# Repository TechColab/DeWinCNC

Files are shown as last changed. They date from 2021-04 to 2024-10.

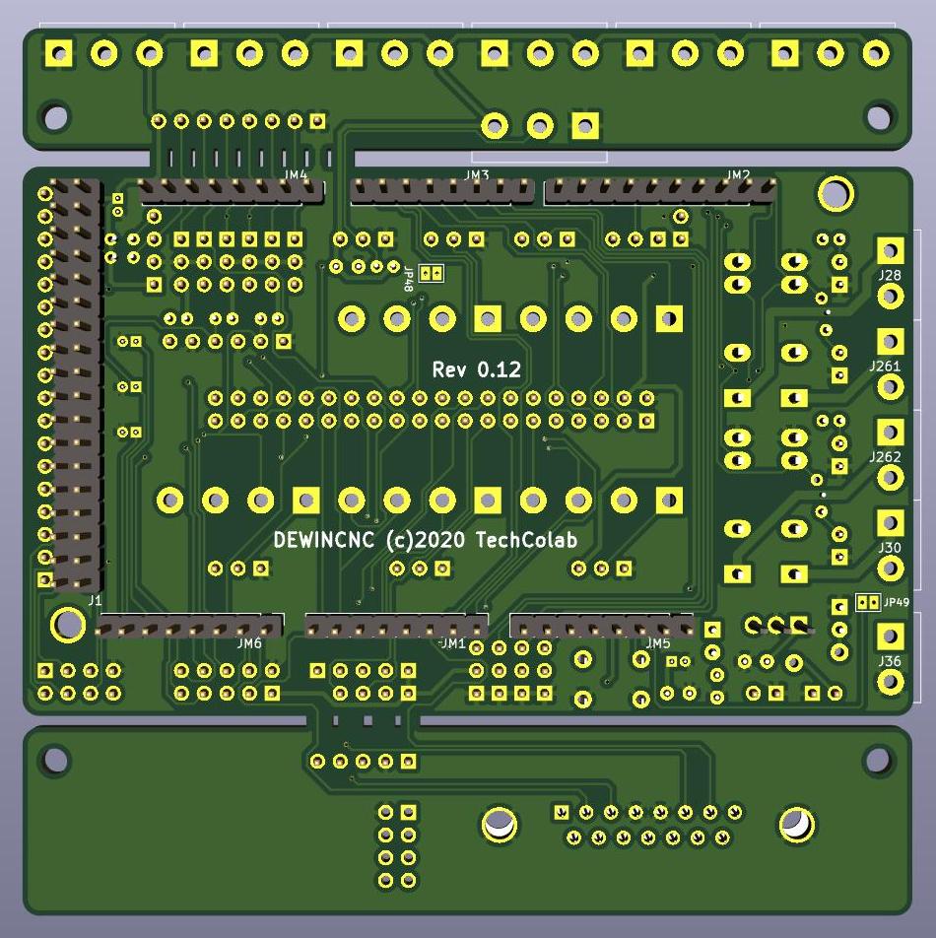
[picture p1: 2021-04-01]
DeWinCNC-B.jpg

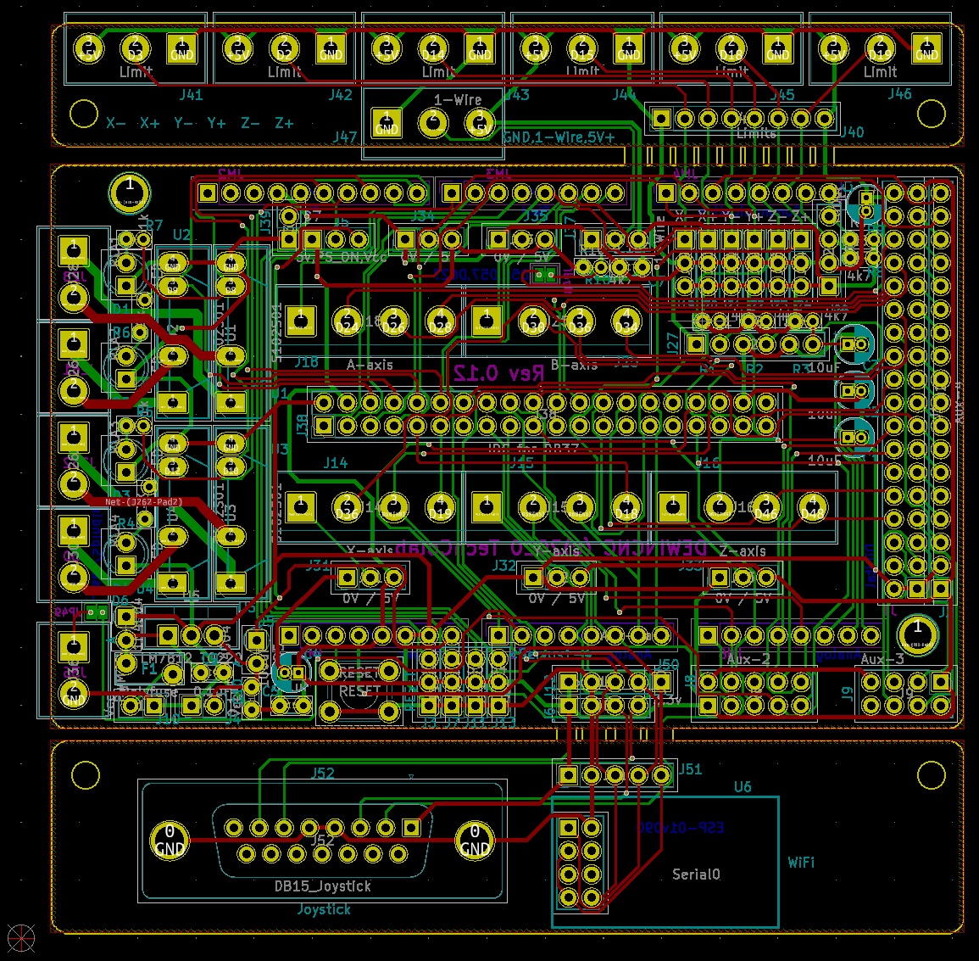
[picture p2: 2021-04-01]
DeWinCNC-PCBjpg.jpg

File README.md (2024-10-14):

DeWinCNC brings the benefits of the RAMPS eco-system to machines which originated with WinCNC.

Compared with WinCNC:
WinCNC software uses a proprietory daughter card on a full-size PCI I/O card which needs a Windows desktop PC.

This shield + an Arduino MEGA 2560 + Marlin firmware enables you to use a laptop of any OS you like, 
with a choice of controller/loader apps.  Or no computer at all - just load files from an SD-card!

You can use entirely open source software with no license or on-going maintenance costs.
Or you can chose somehting like LightBurn which has a great camera feature at a great price.

In common with WinCNC:
Includes the same DB37 plug for direct connection to your existing machne's breakout board.

Compared with RAMPS:
Uses common industrial off-board stepper driver modules so you can scale to any power your mechine needs.

Has a 1-Wire interface so you can use as many digital temperature sensors as you like.

Has 4 on-board isolated SolidState Relays for switching machine power, GasAssist, VacuumPump etc.

Can take power entirely from the USB host, or from a common industrial 24Vdc supply.

Limit switch inputs have convenient screw-terminal connectors.

In common with RAMPS:
Limit switch headers, I2C & reset botton.
Keeps the Aux-1,2,3,4 ports for Servos, SD-card, LCD contoler etc. within the same footprint.

Additional functionality:
Could be plugged into the WinCNC controller to replace the CNC machine's breakout board.
Could be used with the WinCNC controller to monitor/simulate most signals.
Can be used as a general purpose breakout shield with 4 SSRs & 23 I/O lines (inc 10 analog).

ToDo:
Most PCB manufacturers will want a bigger gap between main & break-off boards.  And perforation holes.

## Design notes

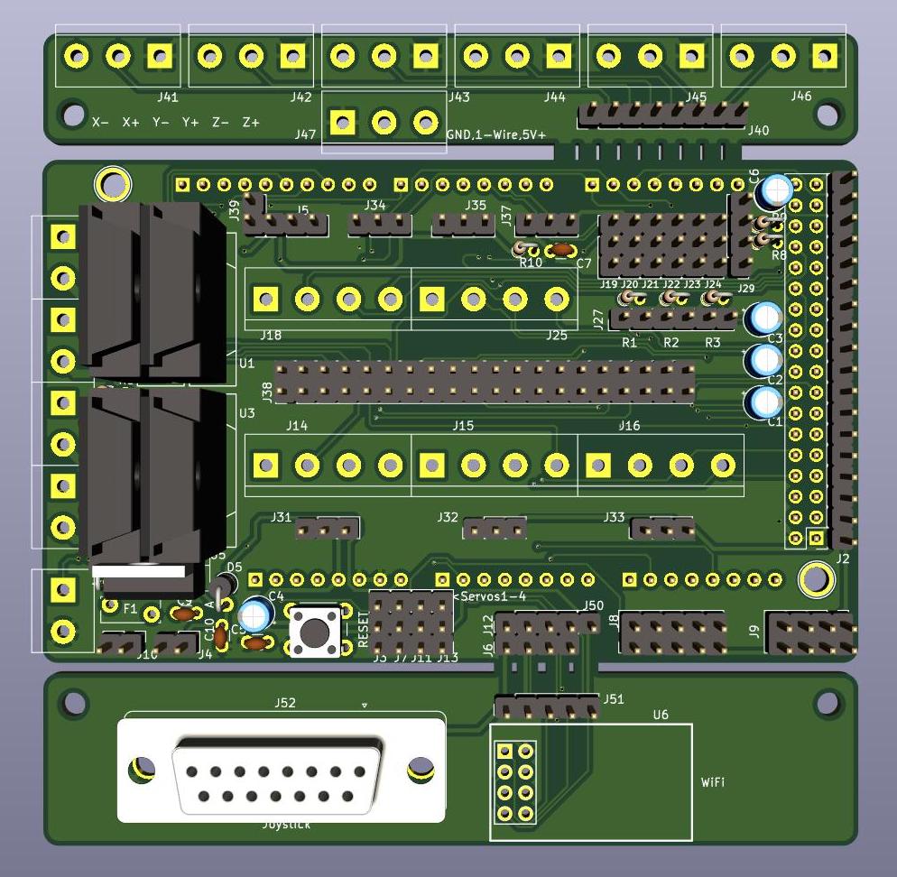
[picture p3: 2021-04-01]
DeWinCNC-F.jpg

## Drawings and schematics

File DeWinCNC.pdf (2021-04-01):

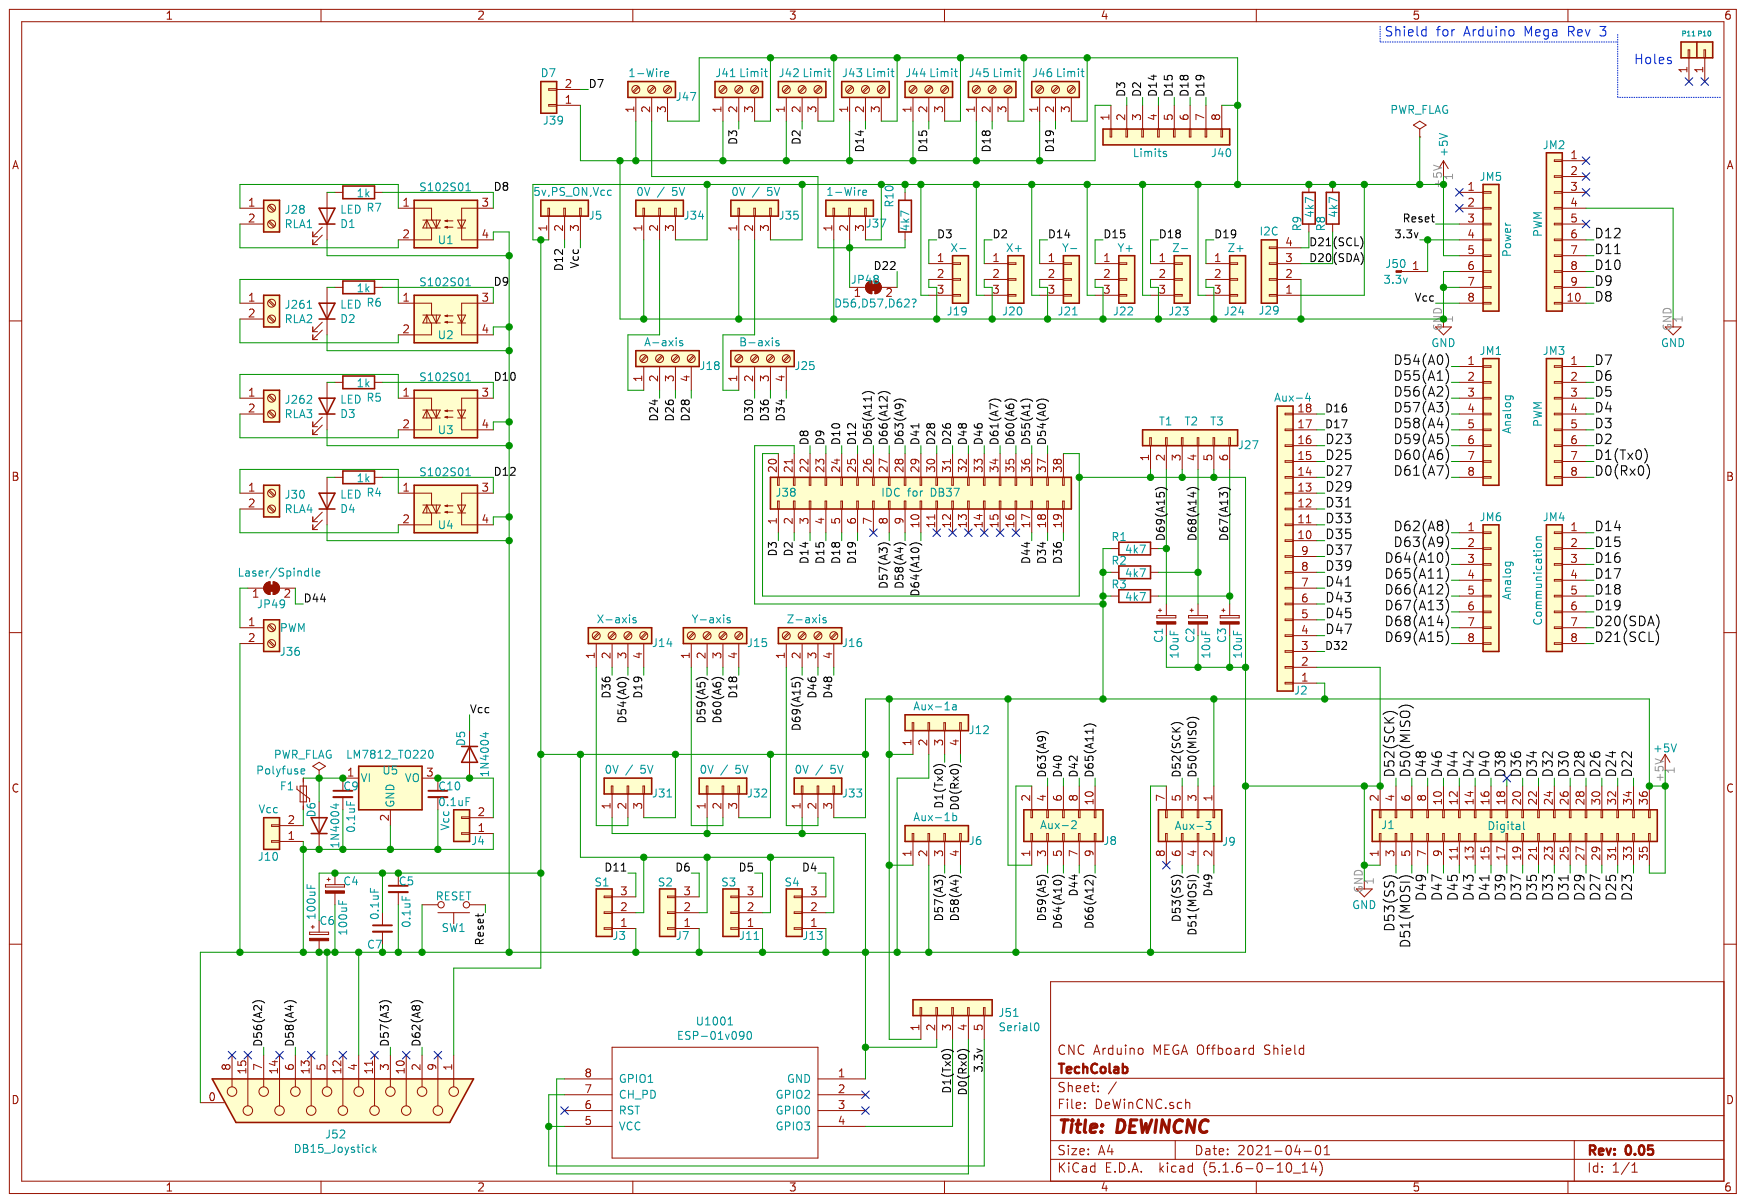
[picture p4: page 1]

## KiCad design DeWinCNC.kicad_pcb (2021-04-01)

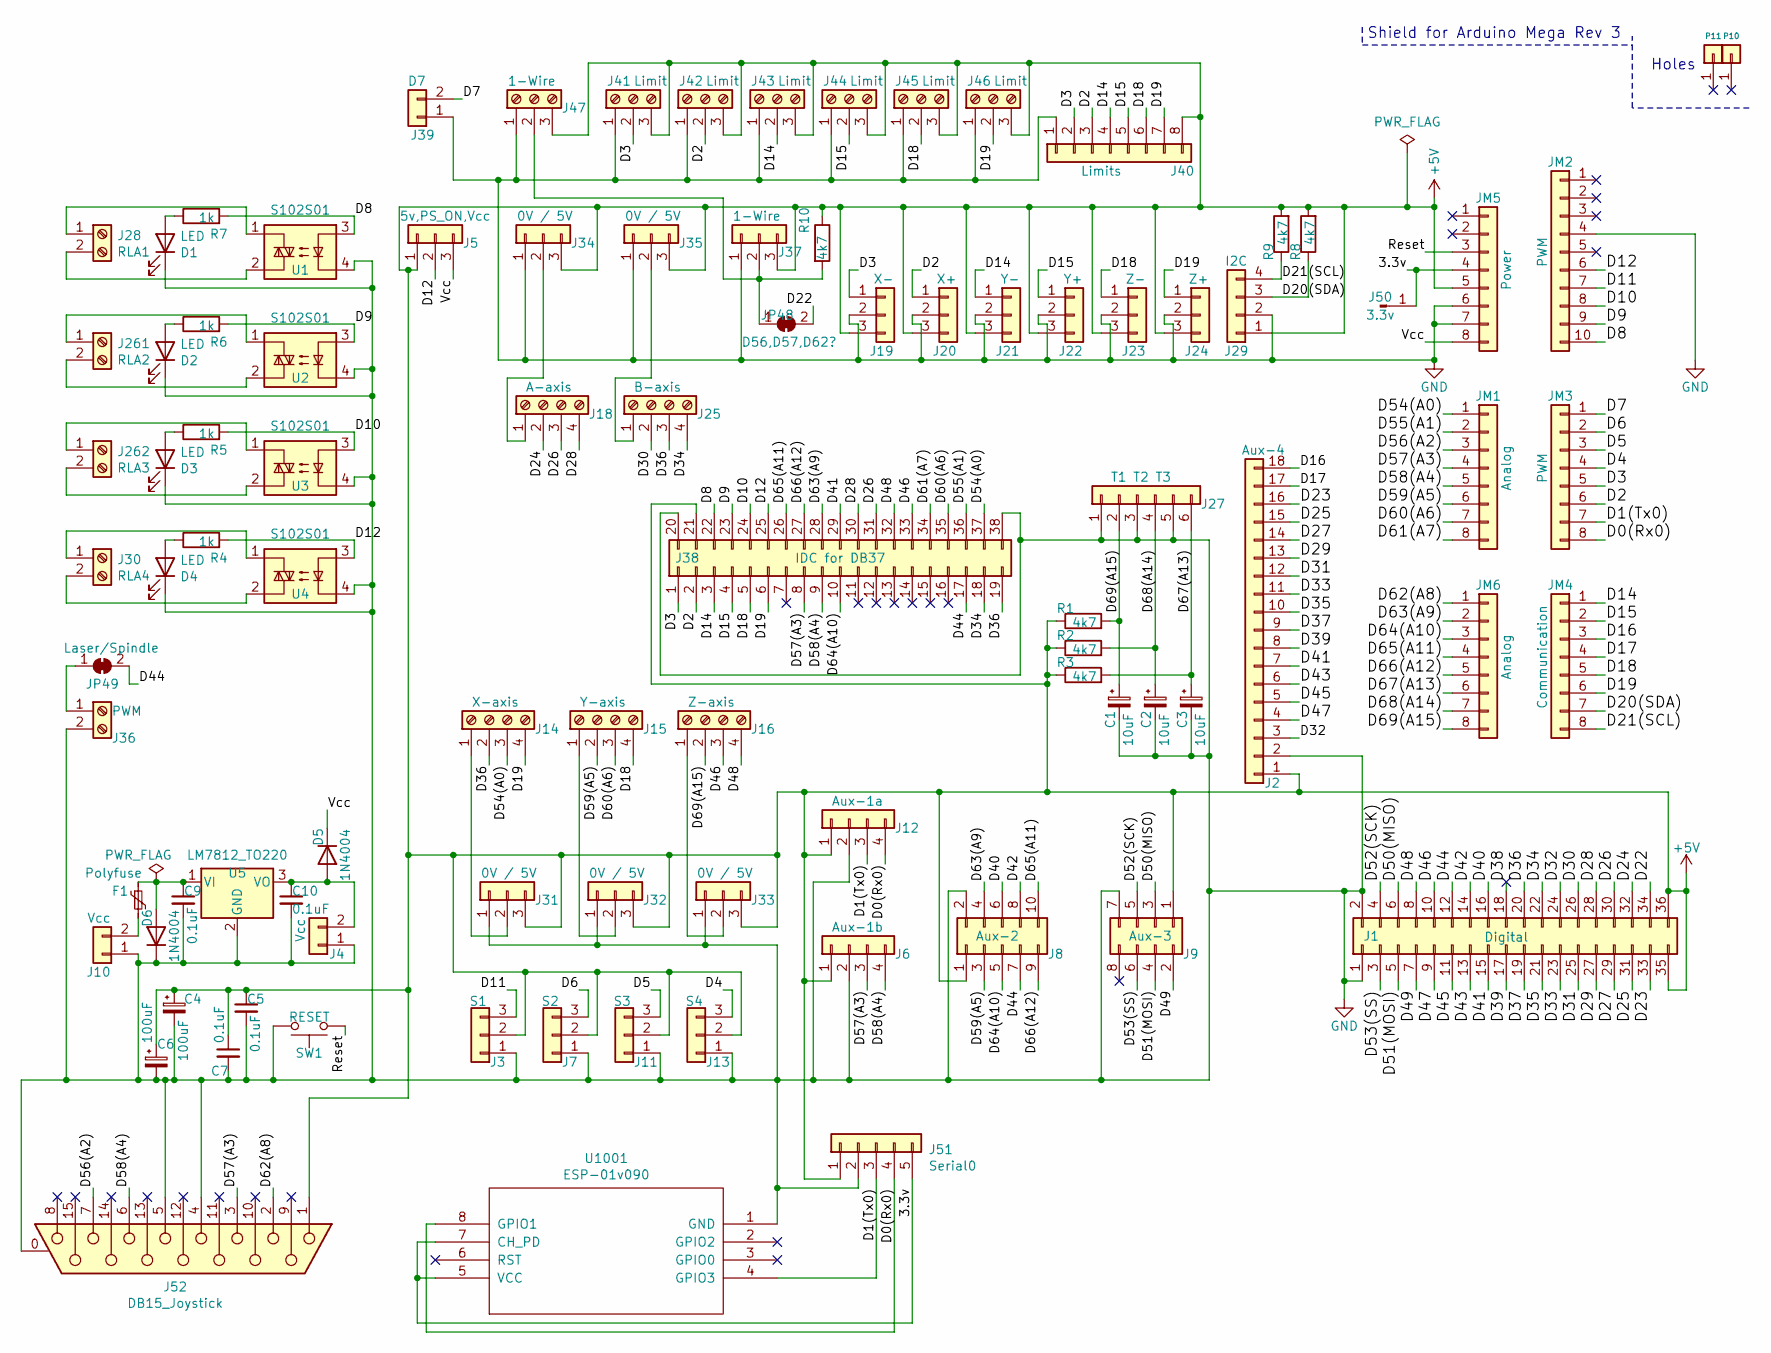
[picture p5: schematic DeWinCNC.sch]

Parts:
C1, C2, C3: 10uF
C4, C6: 100uF
C5, C7, C9, C10: 0.1uF
D1, D2, D3, D4: LED
D5, D6: 1N4004; D_DO-41_SOD81_P10.16mm_Horizontal
F1: Polyfuse
J1: Digital; Socket_Strip_Arduino_2x18
J2: Aux-4
J3: S1
J4, J10: Vcc
J5: 5v,PS_ON,Vcc
J6: Aux-1b
J7: S2
J8: Aux-2
J9: Aux-3
J11: S3
J12: Aux-1a
J13: S4
J14: X-axis
J15: Y-axis
J16: Z-axis
J18: A-axis
J19: X-
J20: X+
J21: Y-
J22: Y+
J23: Z-
J24: Z+
J25: B-axis
J27: T1 T2 T3
J28: RLA1
J29: I2C
J30: RLA4
J31, J32, J33, J34, J35: 0V / 5V
J36: PWM
J37, J47: 1-Wire
J38: IDC for DB37
J39: D7
J40: Limits; Socket_Strip_Arduino_1x08
J41, J42, J43, J44, J45, J46: Limit
J50: 3.3v
J51: Serial0
J52: DB15_Joystick
J261: RLA2
J262: RLA3
JM1, JM6: Analog; Socket_Strip_Arduino_1x08
JM2: PWM; Socket_Strip_Arduino_1x10
JM3: PWM; Socket_Strip_Arduino_1x08
JM4: Communication; Socket_Strip_Arduino_1x08
JM5: Power; Socket_Strip_Arduino_1x08
JP48: D56,D57,D62?
JP49: Laser/Spindle
P10, P11: CONN_01X01; Arduino_1pin
R1, R2, R3, R8, R9, R10: 4k7
R4, R5, R6, R7: 1k
SW1: RESET
U1, U2, U3, U4: S102S01; SIP4_Sharp-SSR_P7.62mm_Straight
U5: LM7812_TO220; TO-220-3_Vertical
U1001: ESP-01v090; PinSocket_2x04_P2.54mm_Vertical

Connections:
+5V: C4.1, C5.1, C6.1, C7.1, J1.35, J1.36, J2.1, J3.2, J5.1, J6.1, J7.2, J8.1, J9.1, J11.2, J12.1, J13.2, J19.3, J20.3, J21.3, J22.3, J23.3, J24.3, J29.1, J31.3, J32.3, J33.3, J34.3, J35.3, J37.3, J38.21, J40.8, J41.3, J42.3, J43.3, J44.3, J45.3, J46.3, J47.3, J51.1, J52.1, JM5.5, R1.1, R2.1, R3.1, R8.2, R9.2, R10.1
/3.3v: J50.1, J51.5, JM5.4, U1001.5 (VCC), U1001.7 (CH_PD); also elsewhere on the board
/D0(Rx0): J12.4, J51.4, JM3.8, U1001.8 (GPIO1); also elsewhere on the board
/D1(Tx0): J12.3, J51.3, JM3.7, U1001.4 (GPIO3); also elsewhere on the board
/D2: J20.1, J38.2, J40.3, J42.2, JM3.6
/D3: J19.1, J38.1, J40.2, J41.2, JM3.5
/D4: J13.3, JM3.4
/D5: J11.3, JM3.3
/D6: J7.3, JM3.2
/D7: J39.2, JM3.1
/D8: J38.22, JM2.10, R7.2, U1.3
/D9: J38.23, JM2.9, R6.2, U2.3
/D10: J38.24, JM2.8, R5.2, U3.3
/D11: J3.3, JM2.7
/D12: J5.2, J38.25, JM2.6, R4.2, U4.3
/D14: J21.1, J38.3, J40.4, J43.2, JM4.1
/D15: J22.1, J38.4, J40.5, J44.2, JM4.2
/D16: J2.18, JM4.3
/D17: J2.17, JM4.4
/D18: J15.4, J23.1, J38.5, J40.6, J45.2, JM4.5
/D19: J14.4, J24.1, J38.6, J40.7, J46.2, JM4.6
/D20(SDA): J29.3, JM4.7, R8.1
/D21(SCL): J29.4, JM4.8, R9.1
/D22: J1.34, JP48.2 (B)
/D23: J1.33, J2.16
/D24: J1.32, J18.2
/D25: J1.31, J2.15
/D26: J1.30, J18.3, J38.31
/D27: J1.29, J2.14
/D28: J1.28, J18.4, J38.30
/D29: J1.27, J2.13
/D30: J1.26, J25.2
/D31: J1.25, J2.12
/D32: J1.24, J2.3
/D33: J1.23, J2.11
/D34: J1.22, J25.4, J38.18
/D35: J1.21, J2.10
/D36: J1.20, J14.2, J25.3, J38.19
/D37: J1.19, J2.9
/D38: J1.18
/D39: J1.17, J2.8
/D40: J1.16, J8.6
/D41: J1.15, J2.7, J38.29
/D42: J1.14, J8.8
/D43: J1.13, J2.6
/D44: J1.12, J8.7, J38.17, JP49.2 (B)
/D45: J1.11, J2.5
/D46: J1.10, J16.3, J38.33
/D47: J1.9, J2.4
/D48: J1.8, J16.4, J38.32
/D49: J1.7, J9.2
/D50(MISO): J1.6, J9.3
/D51(MOSI): J1.5, J9.4
/D52(SCK): J1.4, J9.5
/D53(SS): J1.3, J9.6
/D54(A0): J14.3, J38.37, JM1.1
/D55(A1): J38.36, JM1.2
/D56(A2): J52.7, JM1.3
/D57(A3): J6.3, J38.8, J52.3, JM1.4
/D58(A4): J6.4, J38.9, J52.6, JM1.5
/D59(A5): J8.3, J15.2, JM1.6
/D60(A6): J15.3, J38.35, JM1.7
/D61(A7): J38.34, JM1.8
/D62(A8): J52.2, JM6.1
/D63(A9): J8.4, J38.28, JM6.2
/D64(A10): J8.5, J38.10, JM6.3
/D65(A11): J8.10, J38.26, JM6.4
/D66(A12): J8.9, J38.27, JM6.5
/D67(A13): C3.1, J27.6, JM6.6, R3.2
/D68(A14): C2.1, J27.4, JM6.7, R2.2
/D69(A15): C1.1, J16.2, J27.2, JM6.8, R1.2
/Reset: JM5.3, SW1.1; also elsewhere on the board
/Vcc: D5.1 (K), J5.3, JM5.8
GND: C1.2, C2.2, C3.2, C4.2, C5.2, C6.2, C7.2, C9.2, C10.2, D1.1 (K), D2.1 (K), D3.1 (K), D4.1 (K), D6.1 (K), J1.1, J1.2, J2.2, J3.1, J4.1, J6.2, J7.1, J8.2, J9.7, J10.1, J11.1, J12.2, J13.1, J19.2, J20.2, J21.2, J22.2, J23.2, J24.2, J27.1, J27.3, J27.5, J29.2, J31.1, J32.1, J33.1, J34.1, J35.1, J36.2, J37.1, J38.20, J38.38, J39.1, J40.1, J41.1, J42.1, J43.1, J44.1, J45.1, J46.1, J47.1, J51.2, J52.0 (PAD), J52.4, J52.5, JM2.4, JM5.6, JM5.7, SW1.2, U1.4, U2.4, U3.4, U4.4, U5.2 (GND), U1001.1 (GND); also elsewhere on the board
unnamed: C9.1, D6.2 (A), F1.1, U5.1 (VI)
unnamed: C10.1, D5.2 (A), J4.2, U5.3 (VO)
unnamed: D1.2 (A), R7.1
unnamed: D2.2 (A), R6.1
unnamed: D3.2 (A), R5.1
unnamed: D4.2 (A), R4.1
unnamed: F1.2, J10.2
unnamed: J14.1, J31.2
unnamed: J15.1, J32.2
unnamed: J16.1, J33.2
unnamed: J18.1, J34.2
unnamed: J25.1, J35.2
unnamed: J28.1, U1.1
unnamed: J28.2, U1.2
unnamed: J30.1, U4.1
unnamed: J30.2, U4.2
unnamed: J36.1, JP49.1 (A)
unnamed: J37.2, J47.2, JP48.1 (A), R10.2
unnamed: J261.1, U2.1
unnamed: J261.2, U2.2
unnamed: J262.1, U3.1
unnamed: J262.2, U3.2

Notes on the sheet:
Shield for Arduino Mega Rev 3
Holes

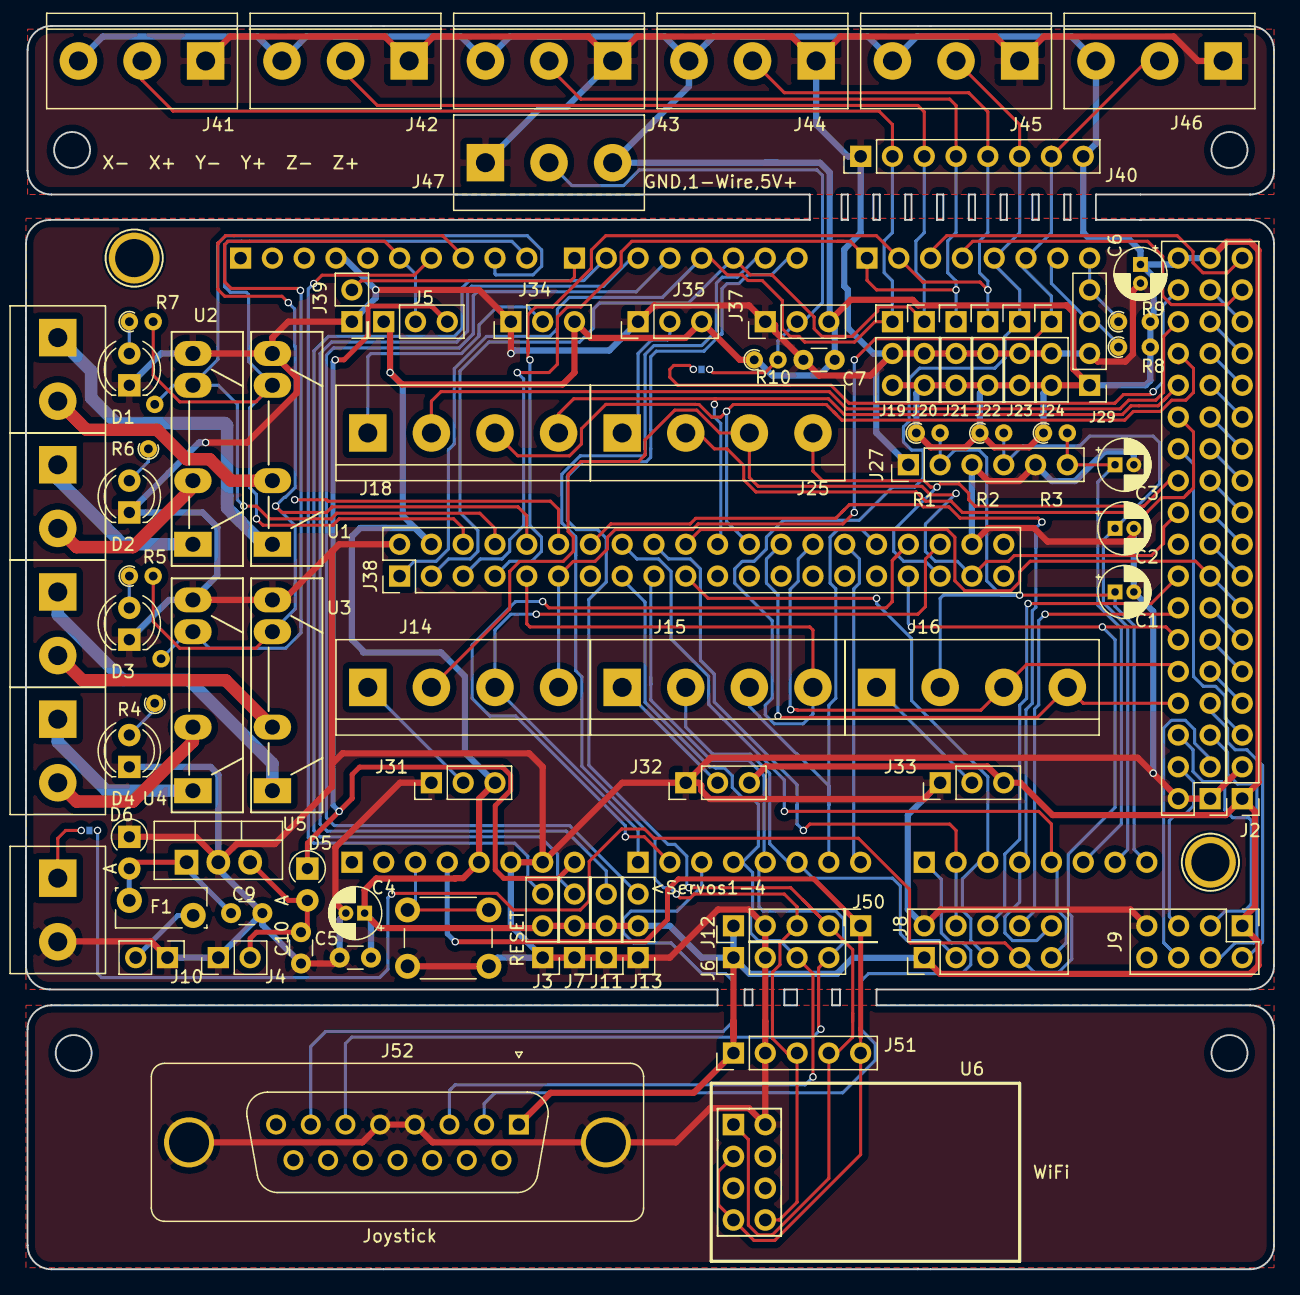
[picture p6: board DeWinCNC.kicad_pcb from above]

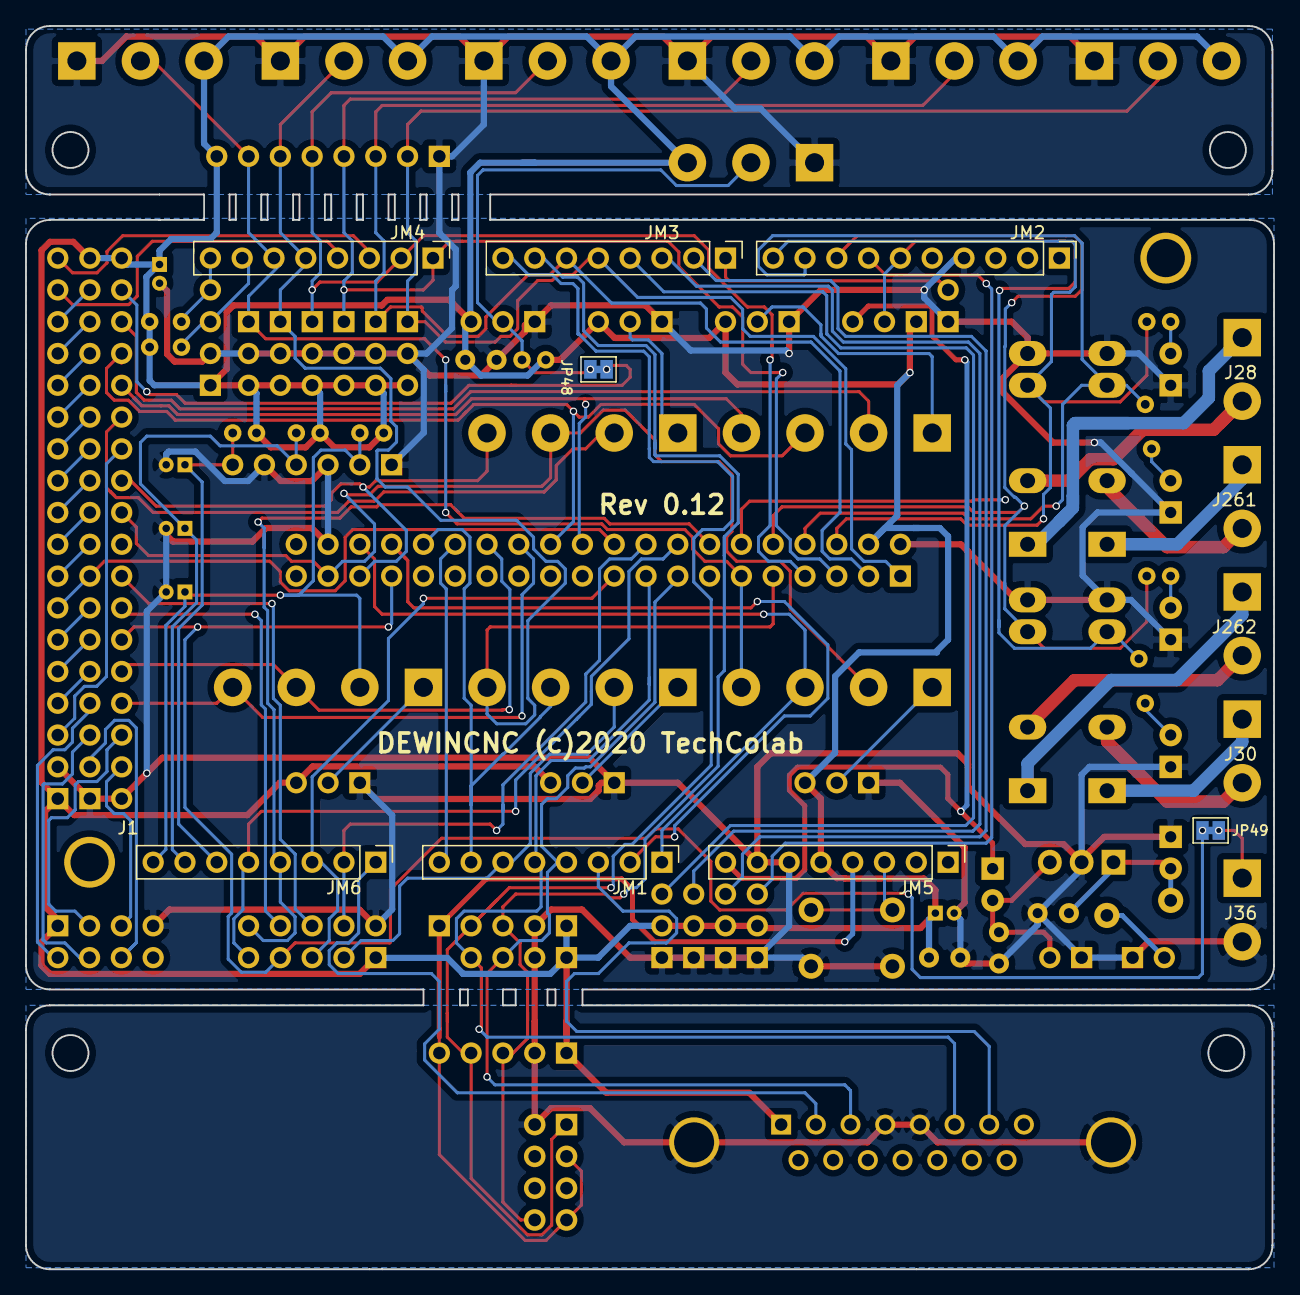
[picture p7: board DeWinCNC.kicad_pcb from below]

Board: 2 copper layers, 99.7 x 99.3 mm, 93 parts (9 on the bottom side), 95 nets.

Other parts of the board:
RESET: RESET; SW_PUSH_6mm_H4.3mm
U6: ESP-01v090; ESP-01

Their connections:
/3.3v: U6.3, U6.7; also elsewhere on the board
/D0(Rx0): U6.1; also elsewhere on the board
/D1(Tx0): U6.8; also elsewhere on the board
/Reset: RESET.1; also elsewhere on the board
GND: RESET.2, U6.2; also elsewhere on the board

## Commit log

2020-10-31 Initial upload
    [DeWinCNC-B_Cu.gbl, DeWinCNC-B_Mask.gbs, DeWinCNC-B_Paste.gbp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]
2021-04-01 Update ESP pinout, round edges more.
    [DeWinCNC-B_Cu.gbl, DeWinCNC-B_Mask.gbs, DeWinCNC-B_Paste.gbp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]

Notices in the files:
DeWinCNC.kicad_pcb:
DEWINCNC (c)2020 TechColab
